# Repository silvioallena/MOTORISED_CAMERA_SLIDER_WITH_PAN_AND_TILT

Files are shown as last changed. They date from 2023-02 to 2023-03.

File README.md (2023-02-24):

# MOTORISED_CAMERA_SLIDER_WITH_PAN_AND_TILT

Thank you to Issac Chasteau and Christoph Lehner for their amazing creations.
This project start from their design and intuitions and my intent was to get the
simplest possible motorised camera slider with pan and tilt features.
Controlled directly via Bluetooth with the help of a Playstation3 or Playstation4 gamepad
and an ESP32 microcontroller.

I tried to follow as much as possible two simple directives: 

- Simplicity of construction and operation
- Use of as few components as possible (Less cost possible)

All coupled with a detailed step-by-step video tutorial in multiple parts.
Especially because no one ever did it !!!

The main structural components that support the filming device need to be 3D printed.
Sorry!

-----------------------VERY IMPORTANT-----------------------------------------------

The libraries and program implemented inside the microcontroller ask for an
ORIGINAL Sony gamepad. 
New or used dosen't matter.
Only 3% to 5% of the "non original" gamepads on any markeplace has compatible
hardware with the libraries.
The developers relied on original Sony hardware for their libraries.
Please don't waste your money.

-----------------------END OF VERY IMPORTANT----------------------------------------

Parts list, schematics, libraries, code will be added to this project Step by Step.

- Tutorial PART 1 Link:

   https://youtu.be/tCjizim1ejc 

- Tutorial PART 2 Link:

   https://youtu.be/ajLDTFrjfqI

   - Tutorial PART 3 Link:

   https://youtu.be/8wd_J_CU_YQ

Project Status:

- 5th  February 2023: Started
- 13th February 2023: Updated 
- 21st February 2023: Ended

<< THE END>> ....

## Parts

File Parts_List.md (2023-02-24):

Parts List:</br>

**Tutorial Part 1:**  (https://youtu.be/tCjizim1ejc)</br>

-25x 6mm diameter spheres for ball bearing</br>
-21x M3 NYLOC NUTS</br>
-10x M3 SQUARED NUTS (THIN!!)</br>
-4x 6x2 NEODYMIUM MAGNETS</br>
-2x  F623ZZ Flange Bearing  3 x 10 x 4</br>
-2x M3 5mm GRUB SCREWS</br>
-9x M3 8mm SOCKET CAP BOLTS/SCREWS</br>
-11x M3 10mm SOCKET CAP BOLTS/SCREWS</br>
-1x M3 14mm SOCKET CAP BOLT/SCREW</br>
-9x M3 18mm SOCKET CAP BOLTS/SCREWS</br>
-1x M3 20mm SOCKET CAP BOLT/SCREWS</br>
-10x M3 WASHERS</br>
-6x M3 16mm COUNTERSUNK SOCKET BOLTS/SCREWS</br>
-2x NEMA 17 42x42x23mm STEPPER MOTORS</br>
-2x A3144 HALL EFFECT SENSORS</br>
</br></br>

**Tutorial Part 2:**  (https://youtu.be/ajLDTFrjfqI)</br>

-15x M3 NYLOC NUTS</br>
-4x M3 12mm SOCKET CAP BOLTS/SCREWS</br>
-3x M3 14mm SOCKET CAP BOLTS/SCREWS</br>
-10x M3 18mm SOCKET CAP BOLTS/SCREWS</br>
-2x M3 30mm SOCKET CAP BOLTS/SCREWS</br>
-10x M3 WASHERS</br></br>
-4x M5 NYLOC NUTS</br>
-4x M5 45mm SOCKET CAP BOLTS/SCREWS</br></br>
-2x PAPER CLIPS MEDIUM SIZE PURE METAL</br>
-1x ONE WAY TOGGLE SWITCH (1.3 x 1 cm)</br>
SWITCH</br>
-4x V-SLOT PULLEY WHEELS WITH BEARINGS (24 x 16 x 10.2)</br>
-1x 2GT TIMING PULLEY 36 TEETH</br>
-2GT TIMING BELT (MINIMUM 2 METERS)</br>
-1x 12V Lithium-Ion Battery (BOSCH GBA12V30 or COMPATIBLE ONE WITH SAME SHAPE)</br></br>

**Tutorial Part 3:**  (https://youtu.be/8wd_J_CU_YQ)</br>

-1x V-SLOT 2080 1500mm -Aluminum Bar (minimum length)</br>
-2x M5 SOCKET CAP BOLTS/SCREWS (minimum 20mm)</br>
-2x T-NUT SPRING LOADED M5 THREADED</br>
-4x T-NUT CONNECTOR M5 THREADED 10cm LONG (minimum: it all depends on how many V-SLOTS you join together)</br>
-16x M5 5mm GRUB SCREWS (minimum: it all depends on how many V-SLOTS you join together)</br>
-1x PCB BOARD (Files for production provided)</br>
-1x 2PIN PCB POWER CONNECTOR</br>
-1x STEP DOWN POWER CONVERTER BUCK MODULE</br>
-1x 2.54mm MALE HEADER SOCKET ROW STRIP</br>
-1x 5,5x2,1 FEMALE PLUG CONNECTOR</br>
-3x 10kOhm 1/4 WATT RESISTORS</br>
-3x 100MF 25V CAPACITORS</br>
-2.54mm FEMALE HEADER SOCKET ROW STRIP (some of them)</br>
-3x XH 2.54 4PIN TERMINAL SOCKET HEADER (MALE)</br>
-3x XH 2.54 3PIN TERMINAL SOCKET HEADER (MALE)</br>
-1x ESP32 DEV KIT C MODULE MICRO CONTROLLER</br>
-3x TMC2209 STEPPER MOTOR DRIVERS
-2x XH 2.54 3PIN TERMINAL PLUG HEADER (FEMALE) and CRIMPED WIRES</br>
-3x XH 2.54 4PIN TERMINAL PLUG HEADER (FEMALE) and CRIMPED WIRES</br></br>

-1x ORIGINAL SONY PS3 GAMEPAD CONTROLLER</br>
or</br>
-1x ORIGINAL SONY PS4 GAMEPAD CONTROLLER</br></br> 

(ALL ALONG THE TUTORIAL)</br>
Super Glue</br>
Wires</br>
Tin Wire (Solder Wire)</br>
Soldering Station or Soldering Iron</br>
Heat Shrinking Tubes</br>

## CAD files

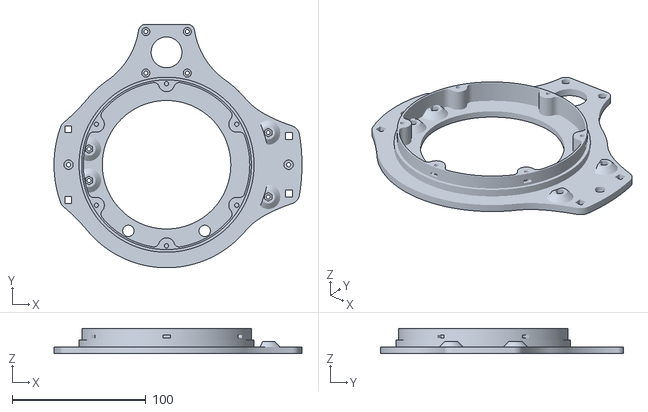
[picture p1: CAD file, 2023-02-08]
STL FILES FOR 3D PRINTER/Main_Base.stl
185.4 x 182.0 x 18.8

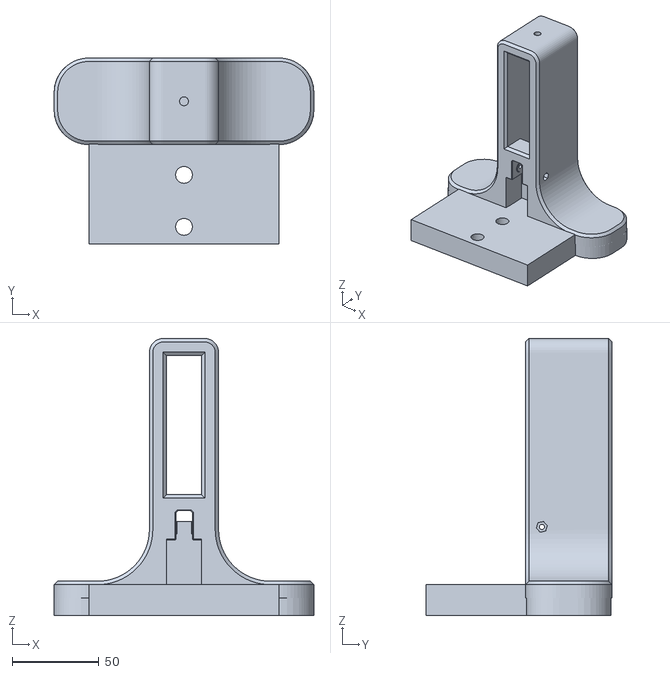
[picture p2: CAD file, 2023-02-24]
STL FILES FOR 3D PRINTER/Foot_REV_2.stl
150.0 x 107.4 x 160.0

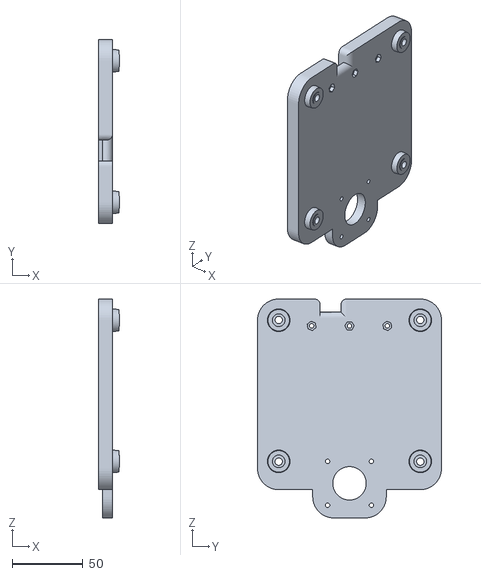
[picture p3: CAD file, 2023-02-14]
STL FILES FOR 3D PRINTER/Slide_Carriage_Motor_Side.stl
15.0 x 130.0 x 154.7

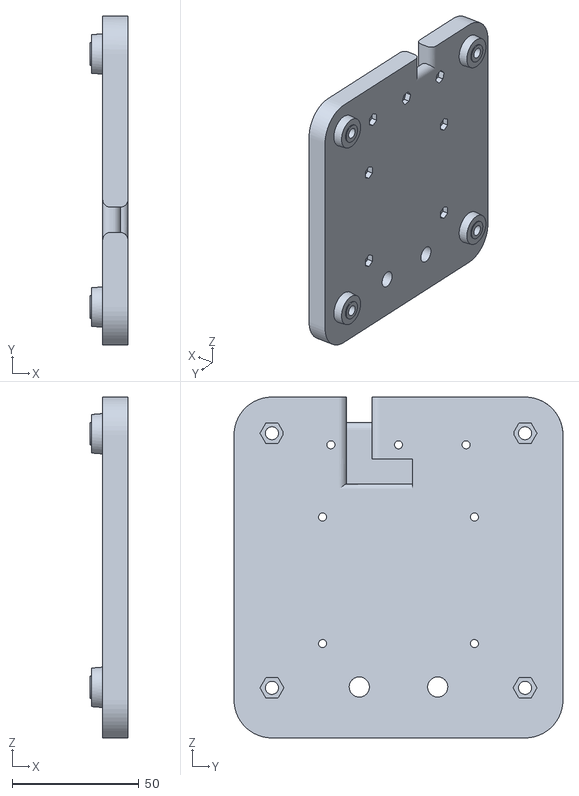
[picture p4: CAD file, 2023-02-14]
STL FILES FOR 3D PRINTER/Slide_Carriage_No_Motor.stl
15.0 x 130.0 x 134.7

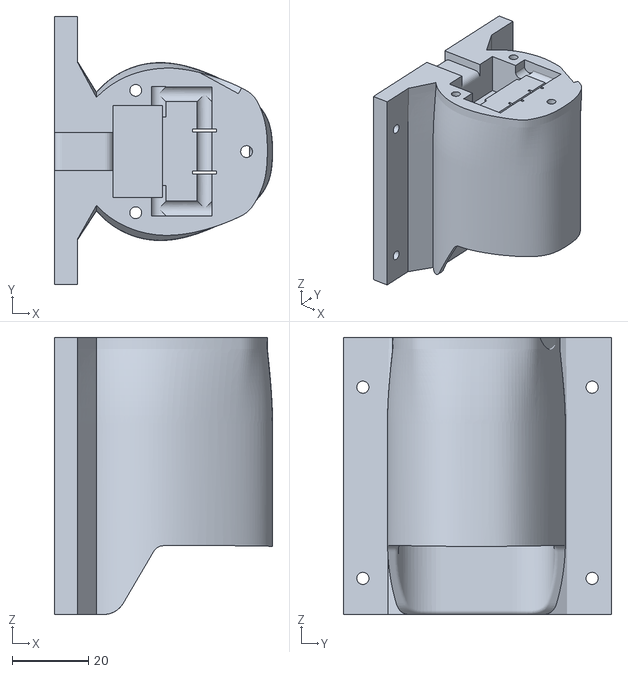
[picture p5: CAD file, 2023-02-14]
STL FILES FOR 3D PRINTER/Battery_Holder.stl
57.1 x 70.0 x 72.5

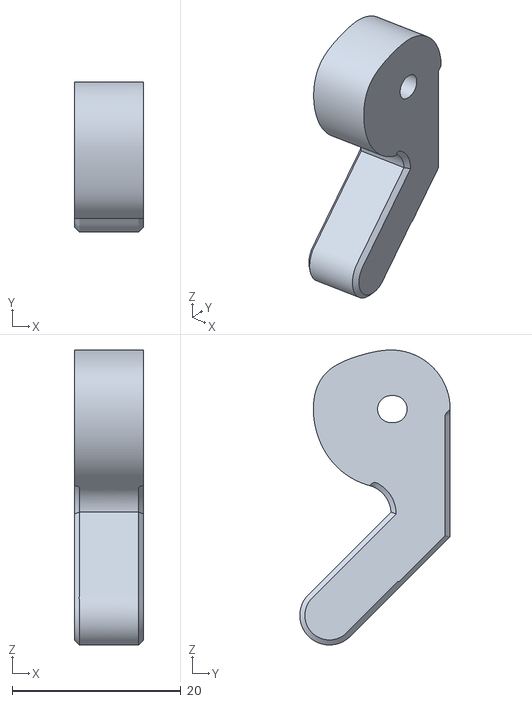
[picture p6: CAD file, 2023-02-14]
STL FILES FOR 3D PRINTER/Belt_Lock.stl
8.20 x 17.8 x 34.9

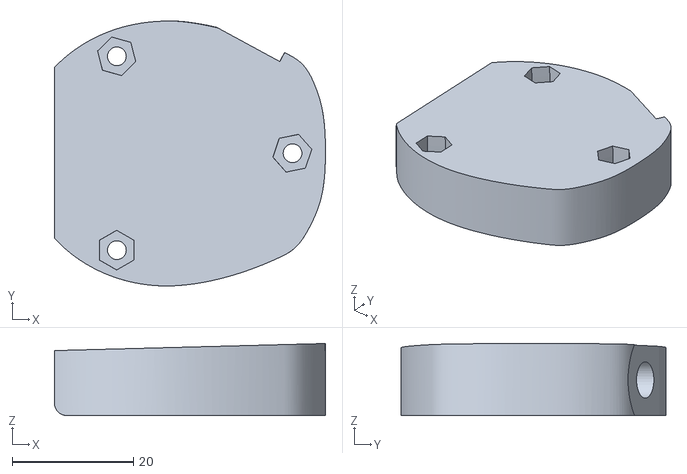
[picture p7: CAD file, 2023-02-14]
STL FILES FOR 3D PRINTER/Battery_Holder_Cover.stl
44.7 x 43.7 x 11.9

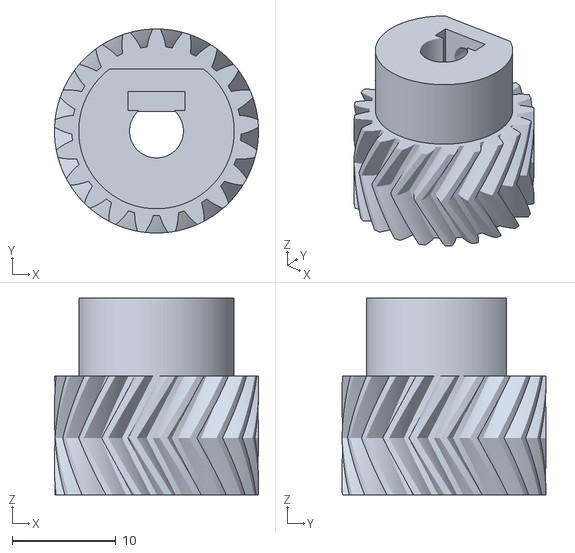
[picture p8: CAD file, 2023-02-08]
STL FILES FOR 3D PRINTER/21_Teeth_Gear_Tilt_Motor.stl
19.7 x 19.7 x 19.0

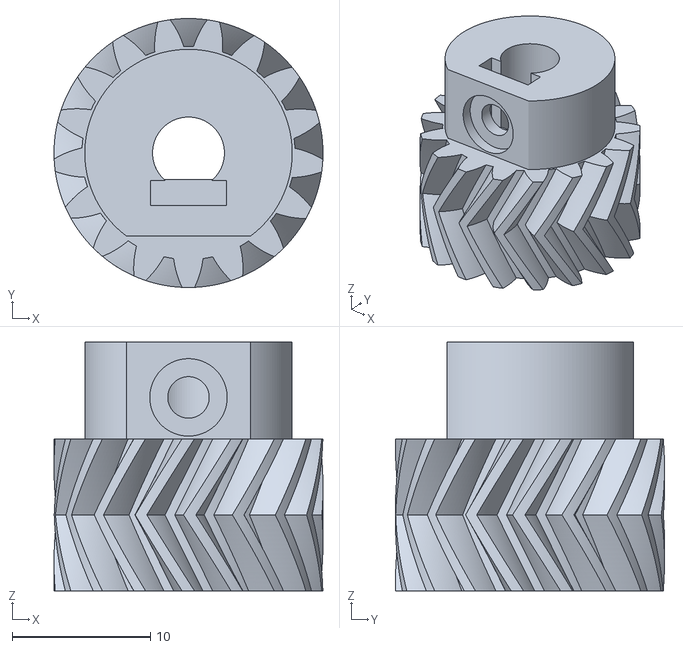
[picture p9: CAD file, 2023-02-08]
STL FILES FOR 3D PRINTER/17_Teeth Gear_Pan_Motor.stl
19.5 x 19.5 x 18.0

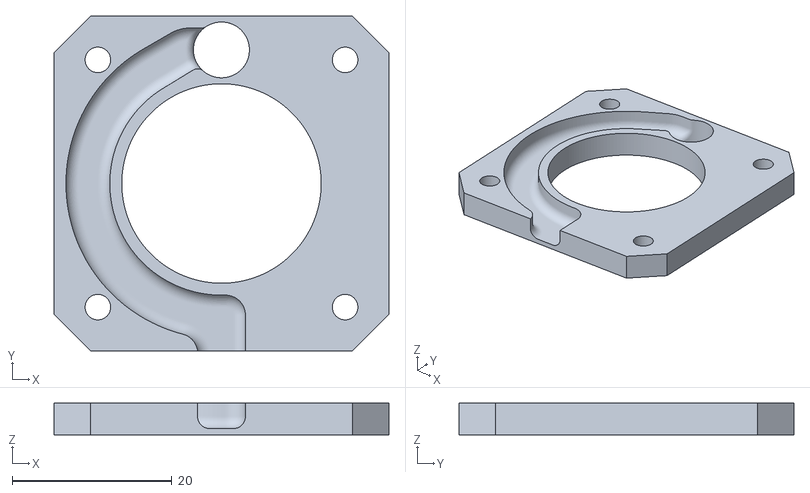
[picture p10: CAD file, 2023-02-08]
STL FILES FOR 3D PRINTER/Motor_Support.stl
42.0 x 42.0 x 4.00

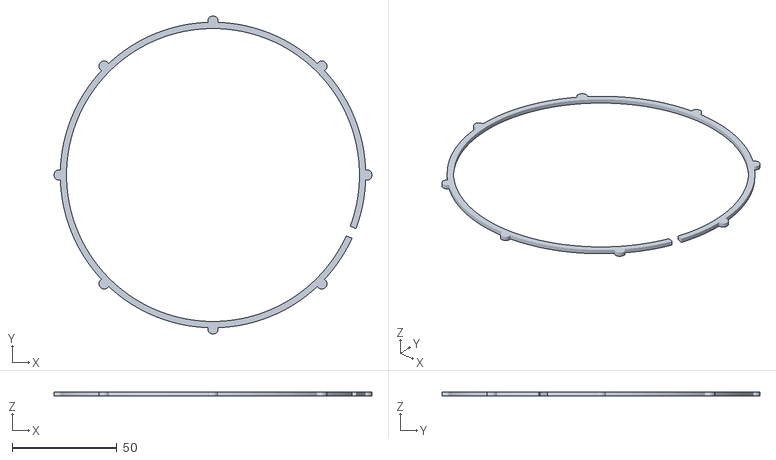
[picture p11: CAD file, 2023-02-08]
STL FILES FOR 3D PRINTER/Bearing_5_Top_Close_Ring.stl
152.0 x 152.0 x 2.00

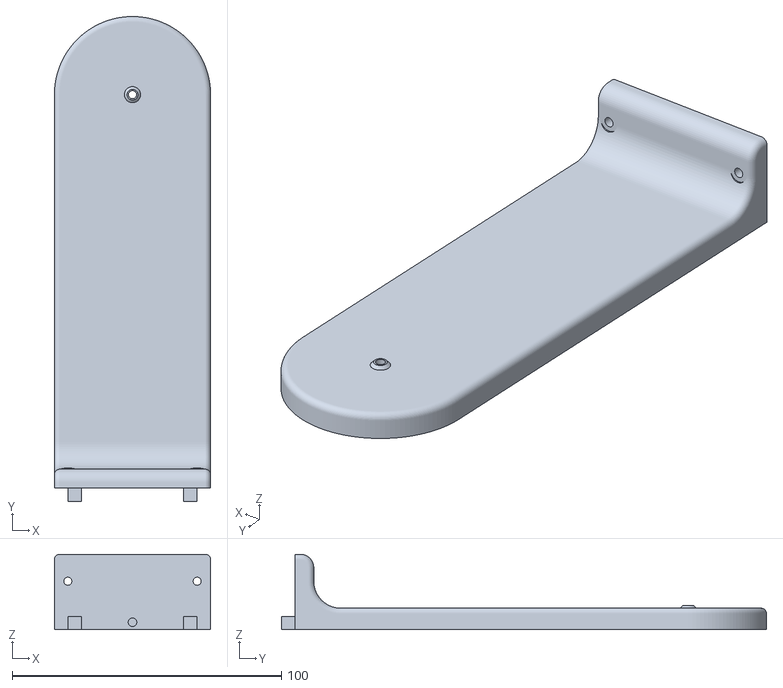
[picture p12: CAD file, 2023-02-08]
STL FILES FOR 3D PRINTER/Lateral_2.stl
58.0 x 180.0 x 28.0

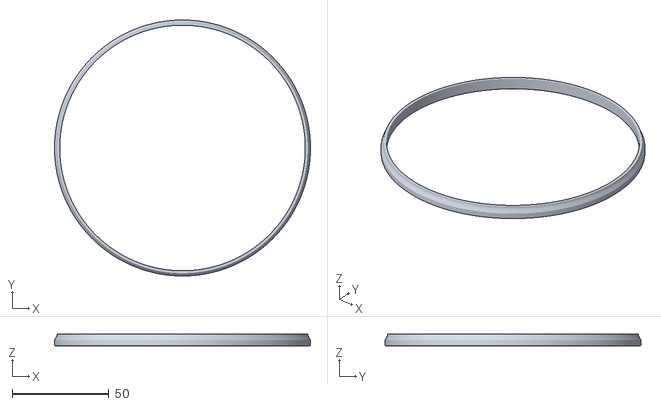
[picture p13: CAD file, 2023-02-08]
STL FILES FOR 3D PRINTER/Bearing_3_Inner_Ring_Half_B.stl
132.4 x 132.4 x 6.35

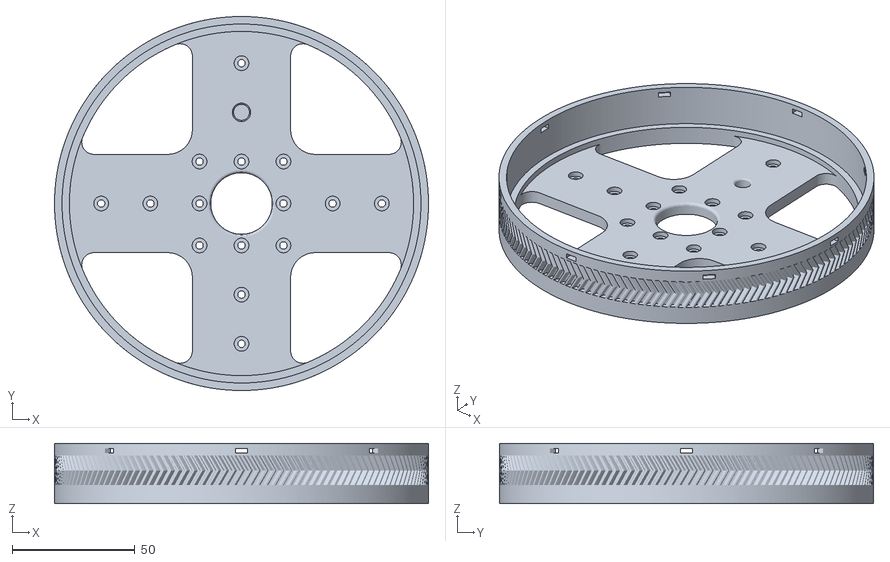
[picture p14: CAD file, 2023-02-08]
STL FILES FOR 3D PRINTER/Circle_Base_144_Teeth.stl
152.1 x 152.1 x 24.5

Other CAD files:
STL FILES FOR 3D PRINTER/Lateral_1.stl
STL FILES FOR 3D PRINTER/Bearing_1_Outer_Ring.stl
STL FILES FOR 3D PRINTER/Net_Clamp.stl
STL FILES FOR 3D PRINTER/Bearing_2_Ball_Retainer_Ring.stl
STL FILES FOR 3D PRINTER/U_Shaped_Camera_Mount.stl

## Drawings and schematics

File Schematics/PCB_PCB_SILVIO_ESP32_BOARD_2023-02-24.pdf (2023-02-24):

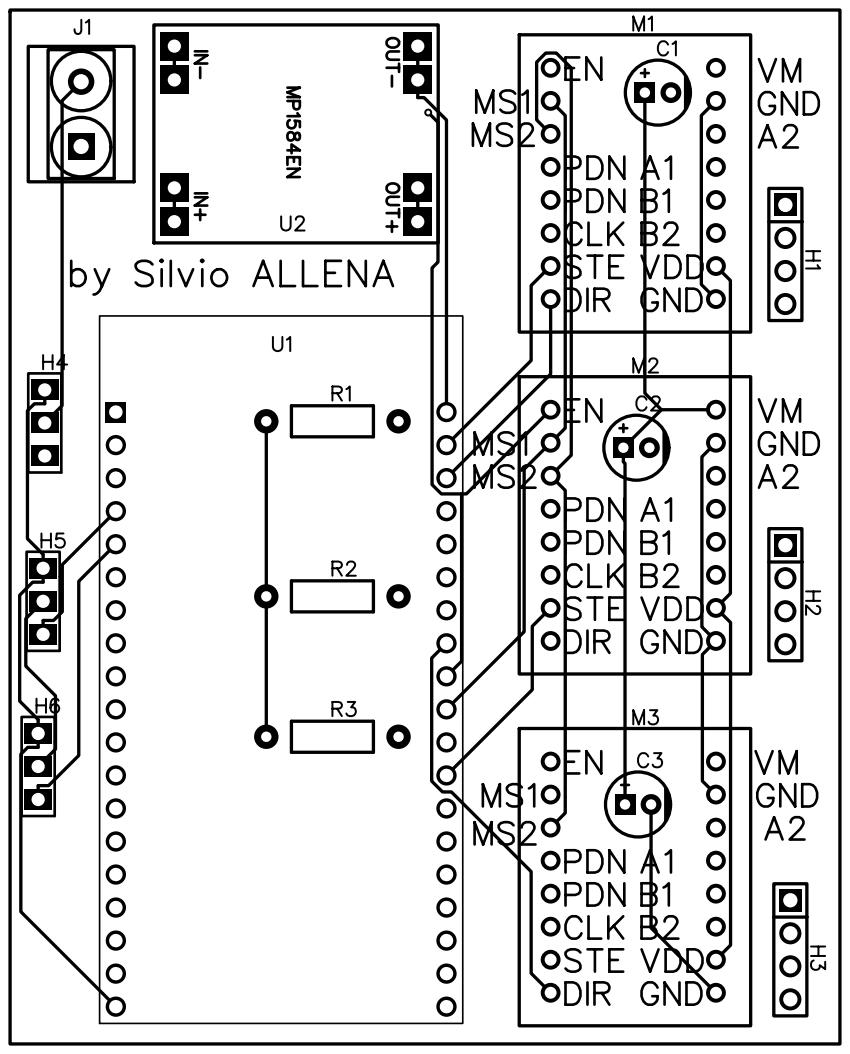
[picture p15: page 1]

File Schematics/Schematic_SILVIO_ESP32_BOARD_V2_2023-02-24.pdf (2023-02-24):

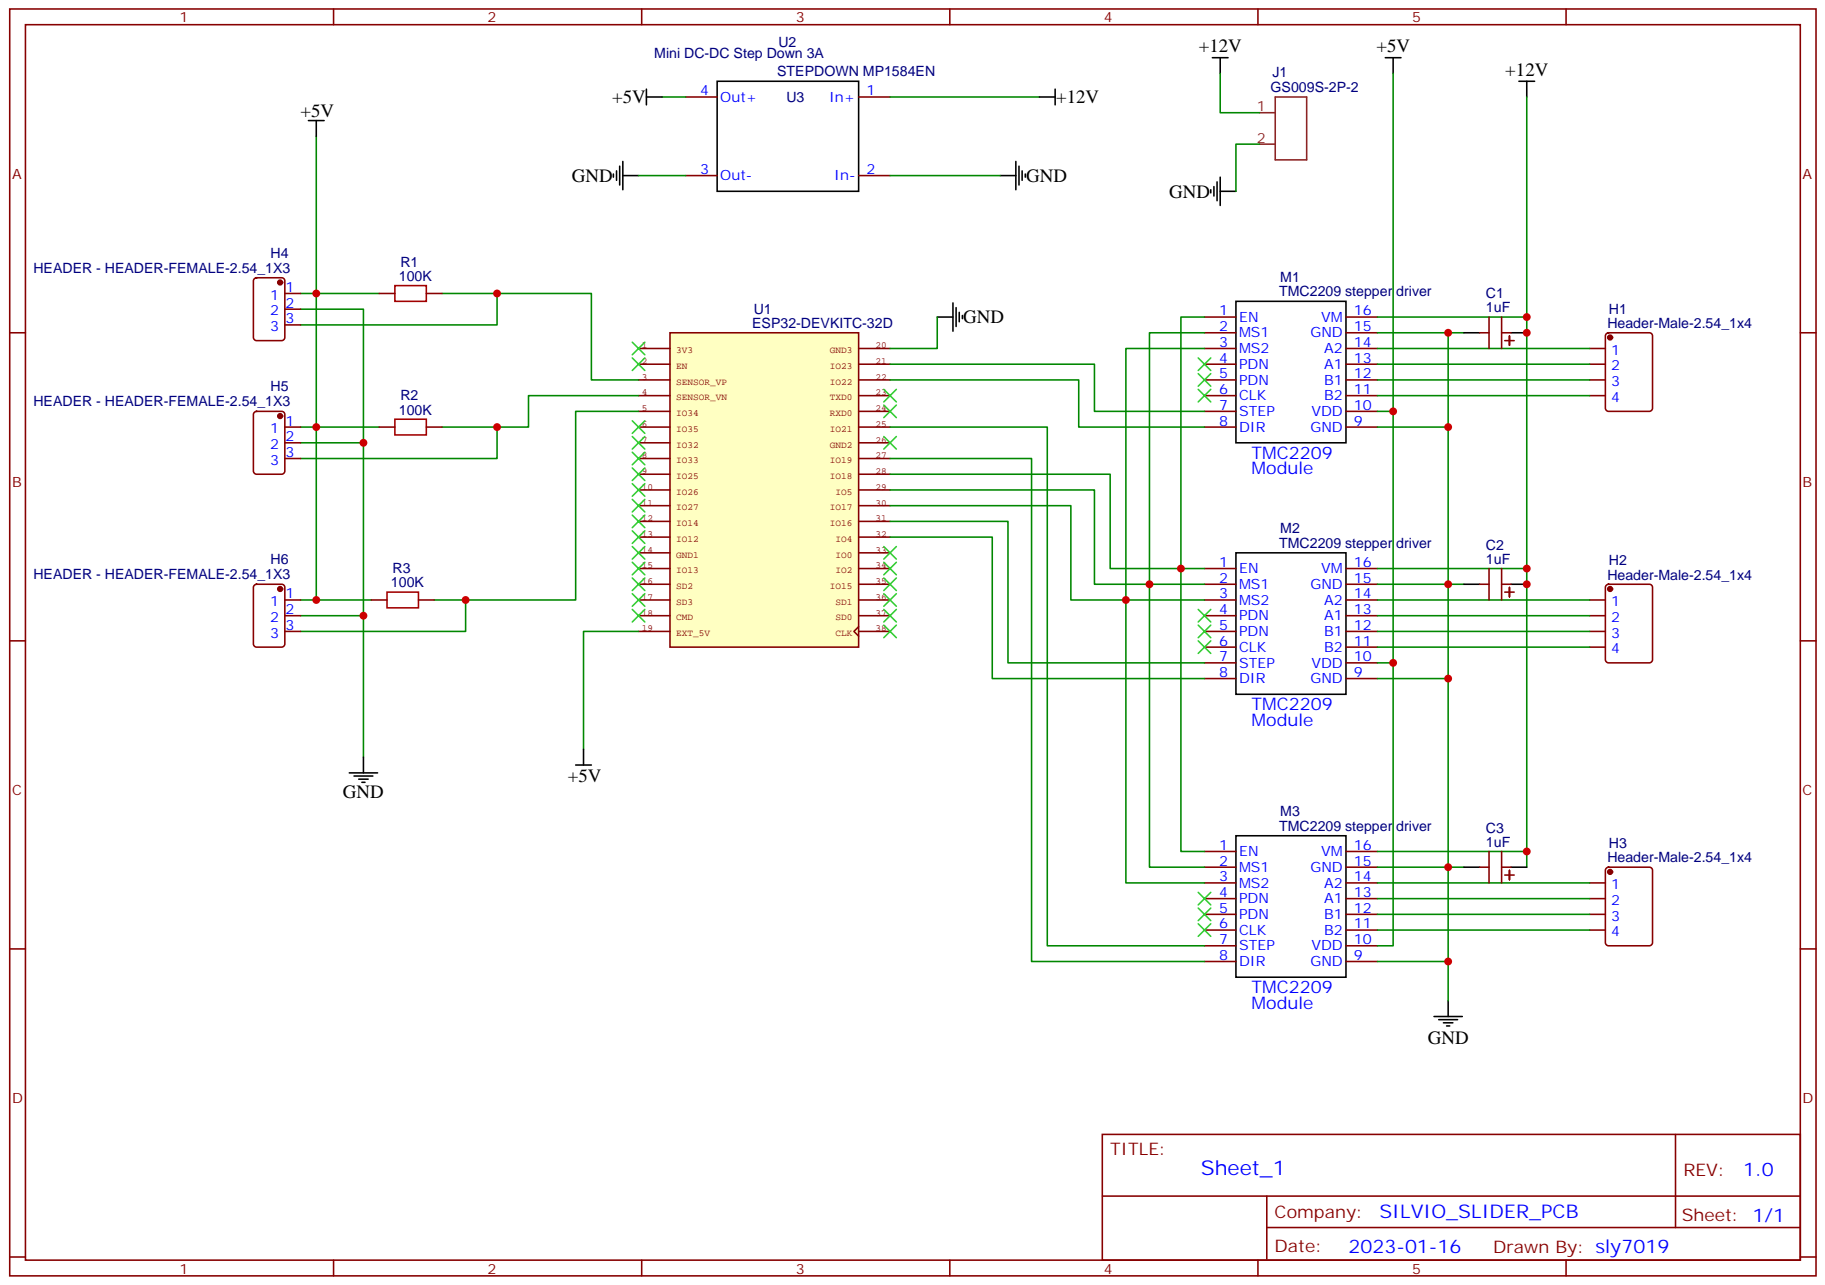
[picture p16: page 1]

Mini DC-DC Step Down 3A

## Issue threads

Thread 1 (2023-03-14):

Arduino sketch

fedeUD1971, 2023-03-14:
Ciao Silvio. Ho visto i tuoi video e quelli di Isaac879. Ottimo lavoro.
Non trovo lo sketch da caricare sulla esp32

silvioallena, 2023-03-14:
Buonasera. Hai perfettamente ragione.
Chiedo scusa per la dimenticanza.
Ho aggiunto la cartella con gli sketch sia per controller PS3 che per controller PS4.
Nel caso avessi dimenticato altro non esitare a farmelo sapere.
Grazie.

silvioallena, 2023-03-14:
Chiedo scusa.
Aggiorno subito il github.

Il giorno mar 14 mar 2023 alle ore 19:39 fedeUD1971 <
***@***.***> ha scritto:

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

Closed 2023-03-16.

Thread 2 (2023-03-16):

ESP32-WROOM32

fedeUD1971, 2023-03-16:
Buongiorno Silvio. La tua PCB può ospitare anche la ESP-WROOM32?

silvioallena, 2023-03-16:
Buongiorno.
Assolutamente sì.
Quella che ho usato è appunto una WROOM32.
Più precisamenta questa:
https://www.amazon.it/dp/B08LL7ZH2W

non sempre disponibile però.

Altrimenti va bene anche la seguente:
https://www.amazon.it/dp/B08BTS62L7

Solo che nel secondo caso i pedini vanno saldati.

Sono delle esp32 dev kit C V4

fedeUD1971, 2023-03-16:
Il problema che la ESP32-WROOM ha 15 piedini per lato, non 19 come quella che hai usato tu

silvioallena, 2023-03-16:
Di ESP32-WROOM ne esistono differenti tipi.
da 30 pin e da 38 pin appunto ed anche altre.

Sullo schema è chiaramente visibile che che la esp32 è una 38 pin ed è anche specificata la versione.
Così come nella lista dei componenti.

Il problema è che l'alimentazione la esp 32 la prende appunto dal PIN 19 sinistro.

Quindi così come è strutturata la PCB inserendo la ESP32 d 30 PIN non prenderebbe tensione e non funzionerebbe quindi.

Ma nella vita c'è sempre una soluzione...

Nello schema così come SULLA PCB ogni punto indicato collegato ai 5V è come se fosse il medesimo punto.

Così come per la terra (GND)

Nella ESP a 30 PIN e in quella a 38 PIN sono appunto queste le due grandi differenze il +5v (o VIN) ed il GND hanno posizioni differenti.

Il resto dei PIN dovrebbe corrispondere in quanto non sono tutti utilizzati.

Quindi se te la senti devi ponticellare esternamente il +5V ed il GND: in altre parole devi usare un cavo sottile volante da un altro punto della PCB.
Ho segnato sulla foto sottostante i punti più vicini

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

e devi saldarli sui relativi pin VIN e GND della ESP.

Avrai comunque due cavi semi volanti sulla PCB.

Va comunque testato non è sicuro al 100%

Non vedo altre alternative se non acquistare una ESP32 WROOM DEV KIT C.

Se mi mandi lo schema dei PIN della tua PCB più tardi controllo se il resto dei PIN è appunto compatibile.

Mi spiace al momento posso proporti solo questa soluzione.

fedeUD1971, 2023-03-23:
Ciao Silvio. Scusa ma ero all'estero per lavoro. Ho ordinato una ESP32 DEV KIT C cosi risolvo il problema.
Ti farò sapere gli esiti. Grazie mille di tutto

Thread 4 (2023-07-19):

Errori per controller ps4

fedeUD1971, 2023-07-19:
Ciao Silvio. copio da Arduino gli errori:
Arduino:1.8.19 (Mac OS X), Scheda:"ESP32 Wrover Module, Default 4MB with spiffs (1.2MB APP/1.5MB SPIFFS), QIO, 80MHz, 921600, None"

/Users/federicobasti/Downloads/MOTORISED_CAMERA_SLIDER_WITH_PAN_AND_TILT-main 4/ARDUINO_SKETCH/FOR_PS4_CONTROLLER/sketch_PS4_CONTROLLER_FEB_19_2023/sketch_PS4_CONTROLLER_FEB_19_2023.ino: In member function 'bool Button::PS4readpin(int)':
sketch_PS4_CONTROLLER_FEB_19_2023:241:39: error: 'struct ps4_button_t' has no member named 'select'
                _value=PS4.data.button.select;
                                       ^
sketch_PS4_CONTROLLER_FEB_19_2023:244:39: error: 'struct ps4_button_t' has no member named 'start'
                _value=PS4.data.button.start;
                                       ^
exit status 1
'struct ps4_button_t' has no member named 'select'

Questo report potrebbe essere più ricco di informazioni abilitando l'opzione
"Mostra un output dettagliato durante la compilazione"
in "File -> Impostazioni"

fedeUD1971, 2023-07-19:
Hai per caso una soluzione?

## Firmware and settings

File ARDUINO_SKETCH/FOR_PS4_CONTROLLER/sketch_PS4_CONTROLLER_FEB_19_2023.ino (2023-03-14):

/*_______________________START LIBRARIES NEEDED BY THE CODE____________________________________*/


#include <ps4.h>
#include <PS4Controller.h>
#include <ps4_int.h>

#include <Arduino.h>
#include "FastAccelStepper.h"
#include "algorithm"

/*_______________________ END LIBRARIES NEEDED BY THE CODE____________________________________*/


/*_______________________START SILVIO VARIABLES____________________________________*/

#define PAN_MOTOR_STEP_PIN 23
#define PAN_MOTOR_DIRECTION_PIN 22
#define TILT_MOTOR_STEP_PIN 16
#define TILT_MOTOR_DIRECTION_PIN 4
#define SLIDE_MOTOR_STEP_PIN 21
#define SLIDE_MOTOR_DIRECTION_PIN 19
#define MOTOR_EN_PIN 18
#define MOTOR_MS1_PIN 5
#define MOTOR_MS2_PIN 17
#define PAN_HALL_PIN 36
#define TILT_HALL_PIN 39
#define SLIDE_HALL_PIN 34
#define PAN_MAX_SPEED 2500
#define PAN_MAX_ACCELERATION 8000
#define TILT_MAX_SPEED 1250
#define TILT_MAX_ACCELERATION 8000
#define SLIDE_MAX_SPEED 7000
#define SLIDE_MAX_ACCELERATION 8000
#define KEYFRAME_ARRAY_LENGTH 10
#define SPEEDADJUSTMENTFACTOR 0.483

/*_______________________START SILVIO AVOID DRIFTING PROBLEMS____________________________________*/



#define INPUT_DEADZONE_LX 120
#define INPUT_DEADZONE_LY 120
#define INPUT_DEADZONE_RX 120
#define INPUT_DEADZONE_RY 120
#define INSTRUCTION_BYTES_SLIDER_PAN_TILT_SPEED 4

bool DEBUG = false;

short shortVals[4] = {0, 0, 0, 0};
short RYShort = 0;
short RXShort = 0;
short LXShort = 0;
short LYShort = 0;
short oldShortVal0 = 0;
short oldShortVal1 = 0;
short oldShortVal2 = 0;
short oldShortVal3 = 0;

bool firstRun = true;


float in_min = -128;          // PS4 DualShock analogue stick Far Left
float in_max = 128;           // PS4 DualShock analogue stick Far Right
float out_min = -255;
float out_max = 255;

/*_______________________END SILVIO AVOID DRIFTING PROBLEMS____________________________________*/


/*_______________________START SILVIO CODE____________________________________*/



unsigned long previousMillis = 0; 
const long debouncedelay = 100; 
float speedfactor=1;
float accelerationfactor=1;
float panspeed_current=0;
float tiltspeed_current=0;
float slidespeed_current=0;
int keyframe_elements = 0;
int current_keyframe_index = -1;
int last_movedto_keyframe_index=-1;
int cntr_moves=0;
int cntr_moves_continous=0;
bool pan_is_moving=true;
bool tilt_is_moving=true;
bool slide_is_moving=true;
long pan_steps_to_move=0;
long tilt_steps_to_move=0;
long slide_steps_to_move=0;
long steps_to_move[3]={0,0,0};
double pan_time_motion_complete=0;
double tilt_time_motion_complete=0;
double slide_time_motion_complete=0;
int pan_speed_motion_complete=0;
int tilt_speed_motion_complete=0;
int slide_speed_motion_complete=0;
bool continous_mode=false;
int delay_continous_mode=0;

struct KeyframeElement {
    long panStepCount = 0;
    float panSpeed = 0;
    long tiltStepCount = 0;
    float tiltSpeed = 0;
    long sliderStepCount = 0;
    float sliderSpeed = 0;
    int msDelay = 0;
};

KeyframeElement keyframe_array[KEYFRAME_ARRAY_LENGTH];

FastAccelStepperEngine engine = FastAccelStepperEngine();
FastAccelStepper *pan_stepper = NULL;
FastAccelStepper *tilt_stepper = NULL;
FastAccelStepper *slide_stepper = NULL;

class Stick {
    private:
        bool _state;
        bool _2ndstate;
        int _pin;
        int _value;

    public:
        Stick(int pin) : _pin(pin) {}
        
        int PS4stickread(int pin2read)
        {
          switch(pin2read)
          {
            case 0:
              _value=PS4.data.analog.stick.lx;
              break;
            case 1:
              _value=PS4.data.analog.stick.ly;
              break;
            case 2:
               _value=PS4.data.analog.stick.rx;
               break;
            case 3:
               _value=PS4.data.analog.stick.ry;
               break;                    
          }          

          if(_value<-1 || _value>1)
          {
            _2ndstate=true;
          }
          if(_value==0 || _value==-1 || _value==1)
          {
            _2ndstate=false;
          }
          return _2ndstate;         
        }

        void begin() 
        {            
            _state = PS4stickread(_pin);
        }

        bool isPressed() 
        {
           bool v = PS4stickread(_pin);
           return v;
           /*
            bool v = PS4stickread(_pin);
            if (v != _state) {
                _state = v;
                if (_state) {
                    return true;
                }
            }
            return false;
            */
        }

        int getValue()
        {
           return _value;

        }
};


/*_______________________MAIN DIFFERENCE WITH PS3 CODE THE BUTTONS ARE NO MORE ANALOG ____________*/

class Button {
    private:
        bool _state;
        bool _2ndstate;
        int _pin;
        int _value;

    public:
        Button(int pin) : _pin(pin) {}
        
        bool PS4readpin(int pin2read)
        {
          switch(pin2read)
          {
            case 0:
              _value=PS4.data.button.up;
              break;
            case 1:
              _value=PS4.data.button.down;
              break;
            case 2:
               _value=PS4.data.button.left;
               break;
            case 3:
               _value=PS4.data.button.right;
               break;
            case 4:
               _value=PS4.data.button.cross;
               break;
            case 5:
               _value=PS4.data.button.square;
               break;
            case 6:
               _value=PS4.data.button.triangle;
               break;
            case 7:
               _value=PS4.data.button.circle;
               break;
            case 8:
               _value=PS4.data.button.l1;
               break;
            case 9:
               _value=PS4.data.button.r1;
               break;
            case 10:
               _value=PS4.data.button.l3;
               break;
            case 11:
               _value=PS4.data.button.r3;
               break;
            case 12:
               _value=PS4.data.button.select;
               break;
            case 13:
               _value=PS4.data.button.start;
               break;
             case 14:
               _value=PS4.data.button.l2;
               break;
            case 15:
               _value=PS4.data.button.r2;
               break;
          }          

          if(_value!=0)
          {
            _2ndstate=true;
          }
          if(_value==0)
          {
            _2ndstate=false;
          }
          return _2ndstate;         
        }

        void begin() 
        {            
            _state = PS4readpin(_pin);
        }

        bool isReleased() 
        {
            bool v = PS4readpin(_pin);
            if (v != _state) {
                _state = v;
                if (_state) {
                    return true;
                }
            }
            return false;
        }
};


/*_______________________POSSIBLE CASES OF WHAT I CAN PRESS ONLY CONSIDER THE NUMBERS____________________________________*/




Button button_dPadUP(0);
Button button_dPadDOWN(1);
Button button_dPadLEFT(2);
Button button_dPadRIGHT(3);
Button button_CROSS(4);
Button button_SQUARE(5);
Button button_TRIANGLE(6);
Button button_CIRCLE(7);
Button button_L1(8);
Button button_R1(9);
Button button_L3(10);
Button button_R3(11);
Button button_SELCET(12);
Button button_START(13);
Button button_L2(14);
Button button_R2(15);

Stick stick_LX(0);
Stick stick_LY(1);
Stick stick_RX(2);
Stick stick_RY(3);


void onConnect() 
{
  Serial.println("Connected.");
}

int add_Position(void) {
  if (keyframe_elements >= 0 && keyframe_elements < KEYFRAME_ARRAY_LENGTH) {
    keyframe_array[keyframe_elements].panStepCount = pan_stepper->getCurrentPosition();
    keyframe_array[keyframe_elements].tiltStepCount = tilt_stepper->getCurrentPosition();
    keyframe_array[keyframe_elements].sliderStepCount = slide_stepper->getCurrentPosition();
    keyframe_array[keyframe_elements].panSpeed = PAN_MAX_SPEED;
    keyframe_array[keyframe_elements].tiltSpeed = TILT_MAX_SPEED;
    keyframe_array[keyframe_elements].sliderSpeed = SLIDE_MAX_SPEED;
    keyframe_array[keyframe_elements].msDelay = 0;

    Serial.print("Pan: "); 
    Serial.println(keyframe_array[keyframe_elements].panStepCount);
    Serial.print("Tilt: "); 
    Serial.println(keyframe_array[keyframe_elements].tiltStepCount);
    Serial.print("Slide: "); 
    Serial.println(keyframe_array[keyframe_elements].sliderStepCount);

    current_keyframe_index = keyframe_elements;
    keyframe_elements++;    
    Serial.print("Added at index: ");    
    Serial.println(current_keyframe_index);
    return 0;
  }
  else {
    Serial.println("Max number of keyframes reached");    
  }
  return -1;
}

void set_Speed(char _pts)
{
   switch(_pts)
   {
      case 'p':
      {
         pan_time_motion_complete=double(steps_to_move[2])/double(PAN_MAX_SPEED);
         Serial.print("time to complete pan movement: ");
         Serial.println(pan_time_motion_complete,5);

         pan_speed_motion_complete=PAN_MAX_SPEED;

         tilt_speed_motion_complete=abs(tilt_steps_to_move)/pan_time_motion_complete;
         Serial.print("tilt steps to move: ");
         Serial.println(tilt_steps_to_move);
         Serial.print("tilt speed according to pan: ");
         Serial.println(tilt_speed_motion_complete);

         slide_speed_motion_complete=abs(slide_steps_to_move)/pan_time_motion_complete;
         Serial.print("slide steps to move: ");
         Serial.println(slide_steps_to_move);
         Serial.print("slide speed according to pan: ");
         Serial.println(slide_speed_motion_complete);


         break;
      }
      case 't':
      {
         tilt_time_motion_complete=double(steps_to_move[2])/double(TILT_MAX_SPEED);
         Serial.print("time to complete tilt movement: ");
         Serial.println(tilt_time_motion_complete,5);

         tilt_speed_motion_complete=TILT_MAX_SPEED;

         pan_speed_motion_complete=abs(pan_steps_to_move)/tilt_time_motion_complete;
         Serial.print("pan steps to move: ");
         Serial.println(pan_steps_to_move);
         Serial.print("pan speed according to tilt: ");
         Serial.println(pan_speed_motion_complete);

         slide_speed_motion_complete=abs(slide_steps_to_move)/tilt_time_motion_complete;
         Serial.print("slide steps to move: ");
         Serial.println(slide_steps_to_move);
         Serial.print("slide speed according to tilt: ");
         Serial.println(slide_speed_motion_complete);

         break;
      }
      case 's':
      {
         slide_time_motion_complete=double(steps_to_move[2])/double(SLIDE_MAX_SPEED);
         Serial.print("time to complete slide movement: ");
         Serial.println(slide_time_motion_complete,5);

         slide_speed_motion_complete=SLIDE_MAX_SPEED;

         pan_speed_motion_complete=abs(pan_steps_to_move)/slide_time_motion_complete;
         Serial.print("pan steps to move: ");
         Serial.println(pan_steps_to_move);
         Serial.print("pan speed according to slide: ");
         Serial.println(pan_speed_motion_complete);

         tilt_speed_motion_complete=abs(tilt_steps_to_move)/slide_time_motion_complete;
         Serial.print("tilt steps to move: ");
         Serial.println(tilt_steps_to_move);
         Serial.print("tilt speed according to slide: ");
         Serial.println(tilt_speed_motion_complete);

         break;

      }
   }

}
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
void loop() 
{
   // only runs code, if the controller is connected, otherwise everything stops
   if(PS4.isConnected())
   {

       if(continous_mode)
         { 
            if(!(pan_stepper->isRunning()) && !(tilt_stepper->isRunning()) && !(slide_stepper->isRunning()) && keyframe_elements>1 )
            {
               delay(delay_continous_mode);
               move_toPosition(cntr_moves_continous);               
               if(keyframe_elements>cntr_moves_continous+1)
               {   
                  cntr_moves_continous++;
               }
               else
               {
                  cntr_moves_continous=0;
               } 
            }   
         }
   
      //debouncing of PS4 input
      unsigned long currentMillis = millis(); 
      if (currentMillis - previousMillis >= debouncedelay) 
      { 
         previousMillis = currentMillis; 



/*____________________________________________________________________________________________________________________________________________________________*/
/*____________________________________________________________________________________________________________________________________________________________*/
/*____________________________________________________________________________________________________________________________________________________________*/


/*___________________________________START SECTION OF THE CODE TO ACOCMODATE SILVIO DEAD ZONE PARAMETERS AND AVOID DRIFTING___________________________________*/
          //STICK INPUT
     
    float LX = (PS4.data.analog.stick.lx);            // Get left analog stick X value
      float LY = (PS4.data.analog.stick.ly);            // Get left analog stick Y value
      float RX = (PS4.data.analog.stick.rx);            // Get right analog stick X value
      float RY = (PS4.data.analog.stick.ry);            // Get right analog stick Y value

      //RX = ((RX - in_min) * (out_max - out_min) / ((in_max - in_min) + out_min));       // Note: "map" alternative

      LX = map(LX, in_min, in_max, out_min, out_max);   // Map DualShock values to (-255 to 255, FF)
      LY = map(LY, in_min, in_max, out_min, out_max);
      RX = map(RX, in_min, in_max, out_min, out_max);
      RY = map(RY, in_min, in_max, out_min, out_max);

      float magnitudeRY = sqrt(RY * RY);                // Get magnitude of Right stick movement to test for DeadZone
    float magnitudeRX = sqrt(RX * RX);                // Get magnitude of Right stick movement to test for DeadZone
      float magnitudeLY = sqrt(LY * LY);                // Get magnitude of Left stick movement to test for DeadZone
      float magnitudeLX = sqrt(LX * LX);                // Get magnitude of Left stick movement to test for DeadZone
     
     
     
     
     
     
     
    if (magnitudeLX > INPUT_DEADZONE_LX) { 
     
         if(stick_LX.isPressed())
         {
            pan_is_moving=true;
      #undef INPUT_DEADZONE_LY
            #define INPUT_DEADZONE_LY 400
      #undef INPUT_DEADZONE_LX
            #define INPUT_DEADZONE_LX 120
      tilt_stepper->stopMove();
               tilt_stepper->setDelayToDisable(65535);
               //tilt_stepper->setSpeedInHz(0);
               tilt_is_moving=false;
      
      
            panspeed_current=speedfactor*PAN_MAX_SPEED*float(0.0078125)*abs(stick_LX.getValue());
            Serial.println("pressed stick_LX");
            Serial.println(stick_LX.getValue());
            pan_stepper->setSpeedInHz(panspeed_current);            
            Serial.println("maxspeed:");
            Serial.println(panspeed_current);

            if(stick_LX.getValue()>1)
            {
               pan_stepper->runForward();
            }
            else
            {
               pan_stepper->runBackward();
            }
         }
         else
         {
            if(pan_is_moving)
            {
               pan_stepper->stopMove();
         #undef INPUT_DEADZONE_LY
               #define INPUT_DEADZONE_LY 120
         //#undef INPUT_DEADZONE_LX
               //#define INPUT_DEADZONE_LX 40
               //pan_stepper->setSpeedInHz(0);
               pan_stepper->setDelayToDisable(65535);
               pan_is_moving=false;
         tilt_stepper->stopMove();
               tilt_stepper->setDelayToDisable(65535);
               //tilt_stepper->setSpeedInHz(0);
               tilt_is_moving=false;
         
            }
            
         }


                                          }
      else {
        if(pan_is_moving)
            {
               pan_stepper->stopMove();
         //#undef INPUT_DEADZONE_LY
               //#define INPUT_DEADZONE_LY 400
         //#undef INPUT_DEADZONE_LX
               //#define INPUT_DEADZONE_LX 120
               //pan_stepper->setSpeedInHz(0);
               pan_stepper->setDelayToDisable(65535);
               pan_is_moving=false;
         
         tilt_stepper->stopMove();
               tilt_stepper->setDelayToDisable(65535);
               //tilt_stepper->setSpeedInHz(0);
               tilt_is_moving=false;
            }                                                        // if in DeadZone, send 0, Don't move
      }



           
     if (magnitudeLY > INPUT_DEADZONE_LY) {    
          
         if(stick_LY.isPressed())
         {
            #undef INPUT_DEADZONE_LX
            #define INPUT_DEADZONE_LX 400
      #undef INPUT_DEADZONE_LY
            #define INPUT_DEADZONE_LY 120
      
      tilt_is_moving=true;
            tiltspeed_current=speedfactor*TILT_MAX_SPEED*float(0.0078125)*abs(stick_LY.getValue());
            Serial.println("pressed stick_LY");
            Serial.println(stick_LY.getValue());
            tilt_stepper->setSpeedInHz(tiltspeed_current);
            Serial.println("maxspeed:");
            Serial.println(tiltspeed_current);

            if(stick_LY.getValue()>1)
            {
               tilt_stepper->runForward();
            }
            else
            {
               tilt_stepper->runBackward();
            }
         }
         else
         {
            if(tilt_is_moving)
            {
               
               tilt_stepper->stopMove();
               
         #undef INPUT_DEADZONE_LX
               #define INPUT_DEADZONE_LX 120
           //#undef INPUT_DEADZONE_LY
                 //#define INPUT_DEADZONE_LY 40
         
         tilt_stepper->setDelayToDisable(65535);
               //tilt_stepper->setSpeedInHz(0);
               tilt_is_moving=false;
         
            }
            
         }


                                          }
      

      else
         {
            if(tilt_is_moving)
            {
               
               tilt_stepper->stopMove();
              //#undef INPUT_DEADZONE_LX
              //#define INPUT_DEADZONE_LX 400
        //#undef INPUT_DEADZONE_LY
              //#define INPUT_DEADZONE_LY 40
         
         
         tilt_stepper->setDelayToDisable(65535);
               //tilt_stepper->setSpeedInHz(0);
               tilt_is_moving=false;
            }
            
         }

 
 
         if (magnitudeRX > INPUT_DEADZONE_RX)           {
    
         if(stick_RX.isPressed())
         {  
            slide_is_moving=true;
            slidespeed_current=speedfactor*SLIDE_MAX_SPEED*float(0.0078125)*abs(stick_RX.getValue());    
            Serial.println("pressed stick_RX");
            Serial.println(stick_RX.getValue());
            slide_stepper->setSpeedInHz(slidespeed_current);
            Serial.println("maxspeed:");
            Serial.println(slidespeed_current);

            if(stick_RX.getValue()>1)
            {
               slide_stepper->runBackward();
            }
            else
            {
               slide_stepper->runForward();
            }
         }
         else
         {
            if(slide_is_moving)
            {
               slide_stepper->stopMove();
               //slide_stepper->setSpeedInHz(0);
               slide_stepper->setDelayToDisable(65535);
               slide_is_moving=false;
            }
            
         }


                                                   }

         else
         {
            if(slide_is_moving)
            {
               slide_stepper->stopMove();
               //slide_stepper->setSpeedInHz(0);
               slide_stepper->setDelayToDisable(65535);
               slide_is_moving=false;
            }

          }

         
     
     if (magnitudeRY > INPUT_DEADZONE_RY)           {

         if(stick_RY.isPressed())
         {
            Serial.println("pressed stick_RY");
            Serial.println(stick_RY.getValue());
         }
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

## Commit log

2023-02-05 Create STL FILES FOR 3D PRINTER
2023-03-14 Create ARDUINO_SKETCH
